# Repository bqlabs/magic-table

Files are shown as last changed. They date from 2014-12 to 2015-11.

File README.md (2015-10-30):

<p align="center">
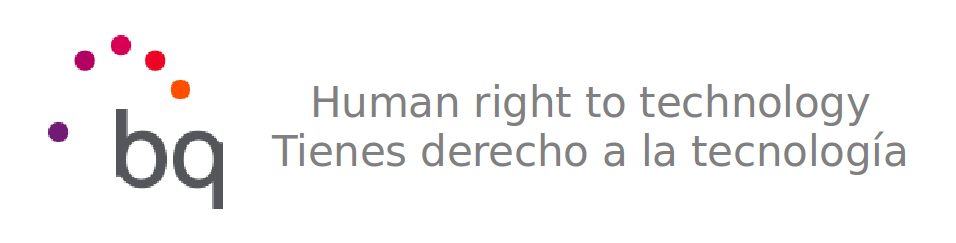
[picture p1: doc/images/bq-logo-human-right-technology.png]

</p>

Magic Table
-------------

HBot-based 2D CNC machine for different applications.

<p align="center">
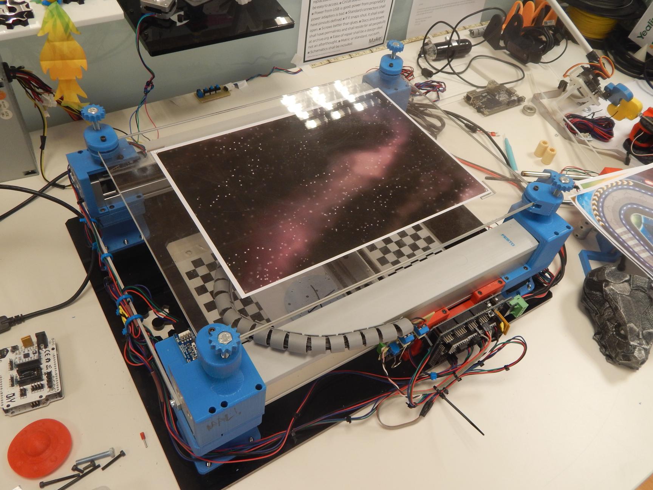
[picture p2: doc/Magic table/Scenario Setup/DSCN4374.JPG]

</p>

# Repository Structure
(Check out each folder's README file for more info on subfolders)

 * /
   * /doc -> Documentation of FESTO hardware parts and tests performed with the machine
   * /firmware ->  Firmware for different embedded devices that that work with the Magic Table
   * /hardware -> Both 3D printable mechanical parts and PCBs for accesories.
   * /software -> Programs to control the Magic Table and use it in different applications.

# Applications developed

## LightPainting
Draw 2D shapes with an RGB light.
<p align="center">
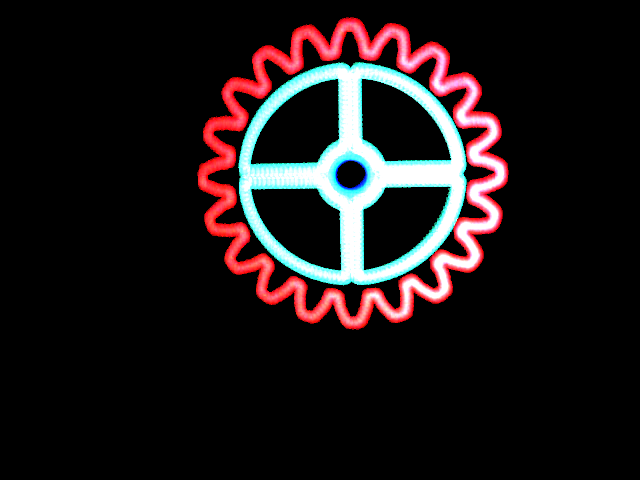
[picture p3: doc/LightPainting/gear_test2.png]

</p>

## Magic Table
Control different pieces and figures with an electromagnet.
<p align="center">
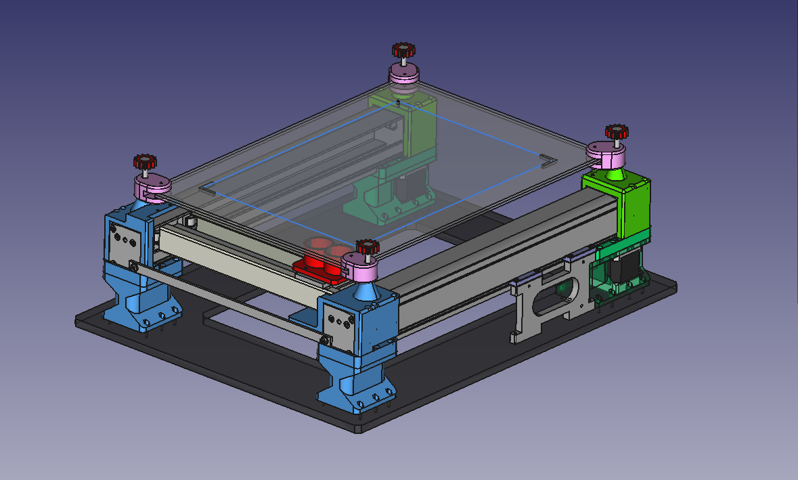
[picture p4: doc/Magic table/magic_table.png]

</p>

# Credits

 * Author: [David Estevez Fernandez](https://github.com/David-Estevez)

# License
<p align="right">

</p>

This machine is licensed under a [Creative Commons Attribution-ShareAlike 4.0 International License](http://creativecommons.org/licenses/by-sa/4.0/). Please read the LICENSE files for more details.

Esta maquina tiene una licencia [Creative Commons Attribution-ShareAlike 4.0 International License](http://creativecommons.org/licenses/by-sa/4.0/). Por favor, lea los ficheros LICENSE para más detalles

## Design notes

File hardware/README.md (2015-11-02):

# Hardware
## Accessories
PCB designs for different accesories, like the etch-a-sketcher or the electromagnet controller board.

## CoreXY Essencials
Set of 3D-printable parts to set the most basic configurations of the magic table

## Light Painting
Set of 3D-printable parts to attach the LED for light paiting applications

## Magic Table
Set of 3D-printable parts to attach the electromagnet and the top cover for the "magic table" applications.

This folder also includes the pieces and backgrounds for each of the "magic table" applications.

## Utils
Different 3D-printable parts to attach accessories such as a webcam to the magic table.

# Z Axis
Set of 3D-printable parts to add a (proof of concept) Z axis.

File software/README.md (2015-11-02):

# Software
## LightPainter
Different Python scripts for light painting applications

## Magic Table
Python software to control the magic table, calibrate it and run demo applications.

It also includes configuration files for each of the applications.

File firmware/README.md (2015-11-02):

# Firmware
## Marlin patch
Patch for Marlin to wait until a position is reached before toggling a GPIO. Instructions to apply the patch can be found inside the folder.

## Etch-a-sketcher
Firmware for the Teensy 3.1 for the "Etch-a-sketcher" peripheral.

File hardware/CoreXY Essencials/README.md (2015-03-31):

# CoreXY Essencials

Parts for the basic CoreXY configuration

## Known bugs

  * The design has an error in the Leg (Upper) BL part, some part that was a dependency was deleted and the dependency is lost. Nevertheless the STL file for that part is correct.

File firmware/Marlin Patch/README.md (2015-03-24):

Patch for Marlin
------------------------

Adds support for waiting for queued movements before toggling GPIOs

To apply patch first clone the Marlin repository:
    $ git clone git@github.com:MarlinFirmware/Marlin.git

Then run the patch command inside the repository:
    $ git am <patch_file>

Note: this patch was applied to commit 512a005. If patching to latest commit fails,
try to patch that one

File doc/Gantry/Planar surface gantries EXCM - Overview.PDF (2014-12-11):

# Overview selected features Planar surface gantry EXCM-30-310-210-KF-W-B-ES

#2226101

Basic configuration
Feature | Value Product type | EXCM series M
Size | 30
Stroke of the X axis | 310 mm
Stroke of the Y-axis | 210 mm
Guide | KF Recirculating ball bearing guide
Motor type | W Without motor
Motor attachment position | B Bottom
Controller | Without
Language of documentation | ES Spanish
03/12/2014 - Subject to change - Festo AG & Co. KG | 1 / 1

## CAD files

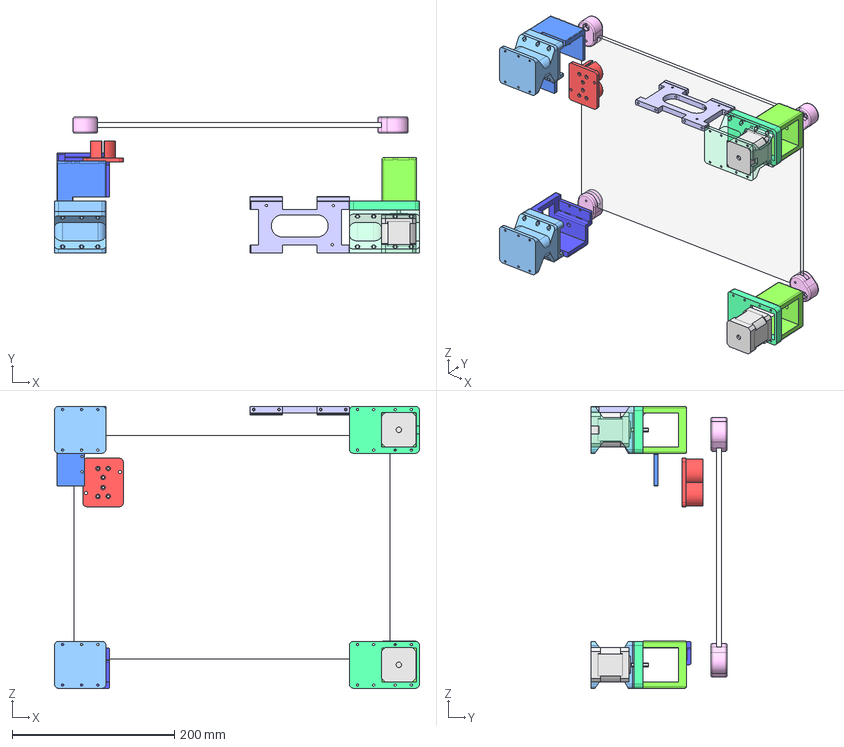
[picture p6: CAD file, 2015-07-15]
hardware/Table Base Holder/Magic Table Assembly.fcstd
450.5 x 168.0 x 348.5 mm
Motor NEMA 17 (47mm) Right
Motor NEMA 17 (40mm) Left
Leg (Upper) Motor [Fillet]
Leg (Body) TR Nice Fillet
Leg (Upper) TR Motor
Leg (Body) BR Nice Fillet
Leg (Upper) BR Endstop holder holes
Leg (Upper) BL [Clone]
Leg (Body) BL Nice Fillet
Arduino Holder Fillet
Support Screw 01 (Top Right)002
Support Up (Top Right)002
Support Screw 02 (Top Right)002
Support Screw 02 (Top Right)001
Support Up (Top Right)001
Support Screw 01 (Top Right)001
Table Holder Base Motor Legs
Clone of Table Holder Base Motor Legs
Table Holder Base Endstop Y
Holder_With_Top_Hole
Magnet_Holder_Hole
Acrylic tabletop (Both)
Attachment
A4 paper
Clone of Attachment
Clone of Attachment001
Clone of Attachment002

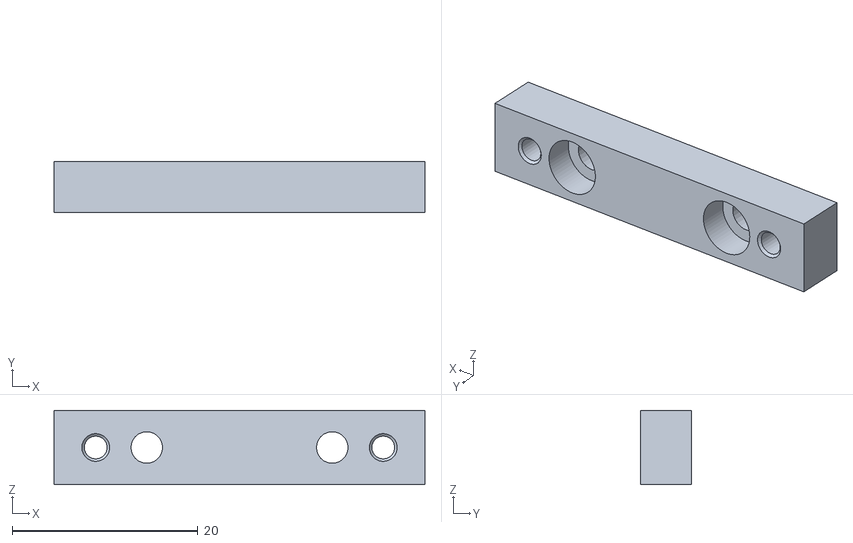
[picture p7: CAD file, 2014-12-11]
doc/Gantry/support_bottom.stl
40.0 x 5.50 x 8.00

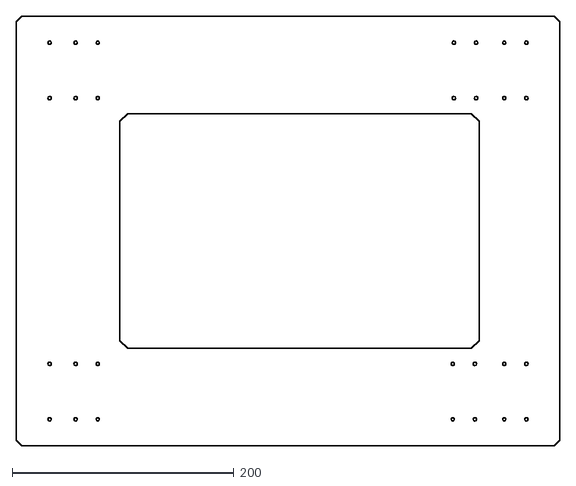
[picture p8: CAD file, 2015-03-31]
hardware/CoreXY Essencials/dxf/base.dxf
490.5 x 388.0

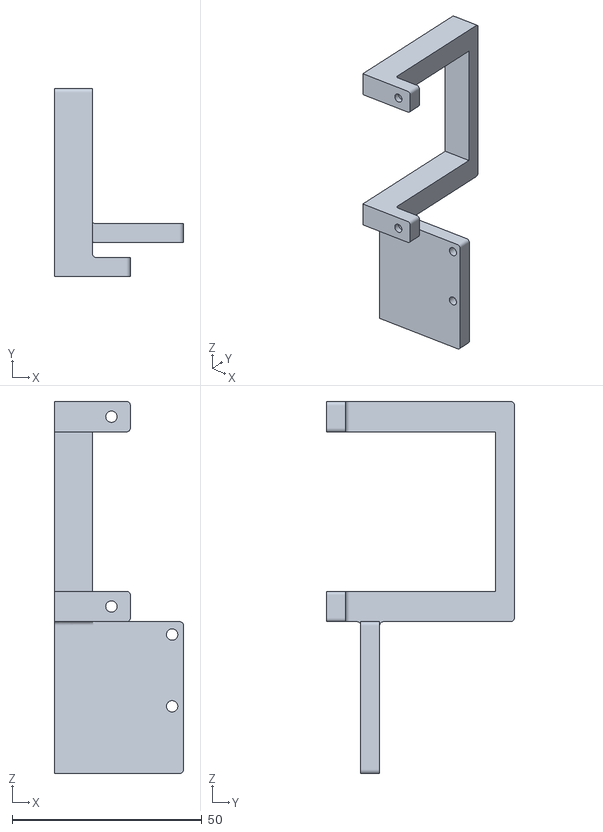
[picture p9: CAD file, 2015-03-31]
hardware/CoreXY Essencials/stl/Endstop Holder Y.stl
34.0 x 49.5 x 98.0

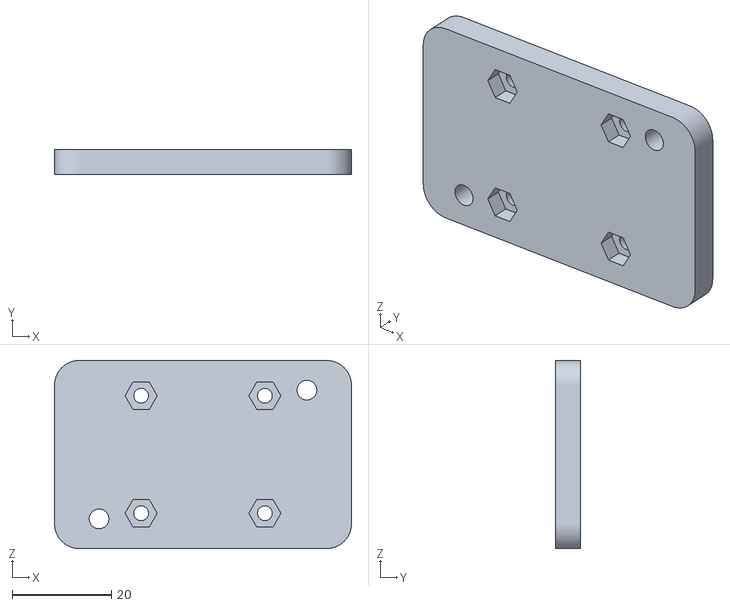
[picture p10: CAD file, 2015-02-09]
hardware/Light Painting/LED holder.stl
60.0 x 5.00 x 38.0

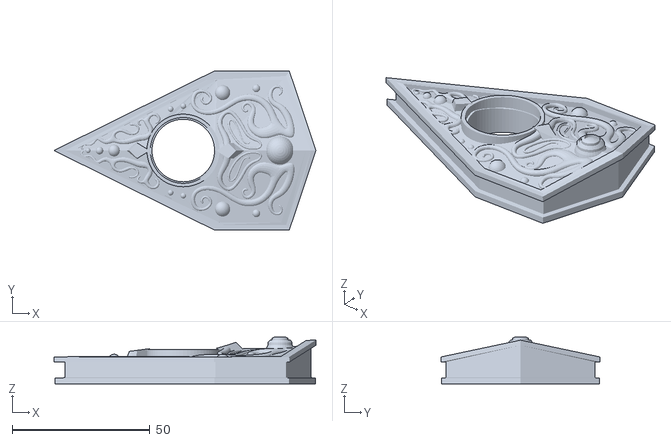
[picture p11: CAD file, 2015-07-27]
hardware/Magic Table/Applications/Ouija/Ouija_Cursor.stl
95.1 x 57.6 x 17.0

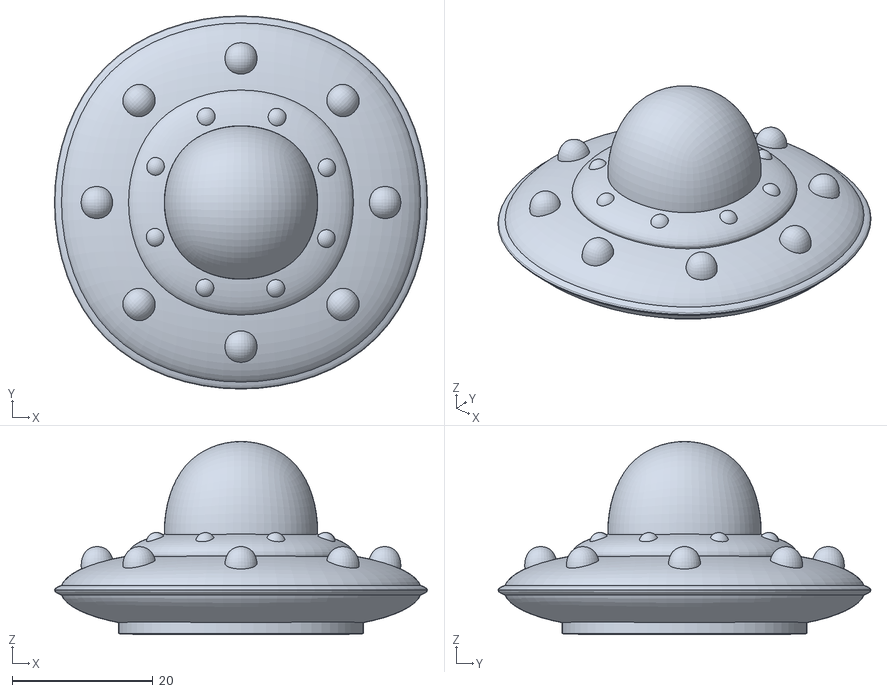
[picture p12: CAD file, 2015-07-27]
hardware/Magic Table/Applications/Space Explorer/UFO.stl
53.0 x 53.0 x 27.5

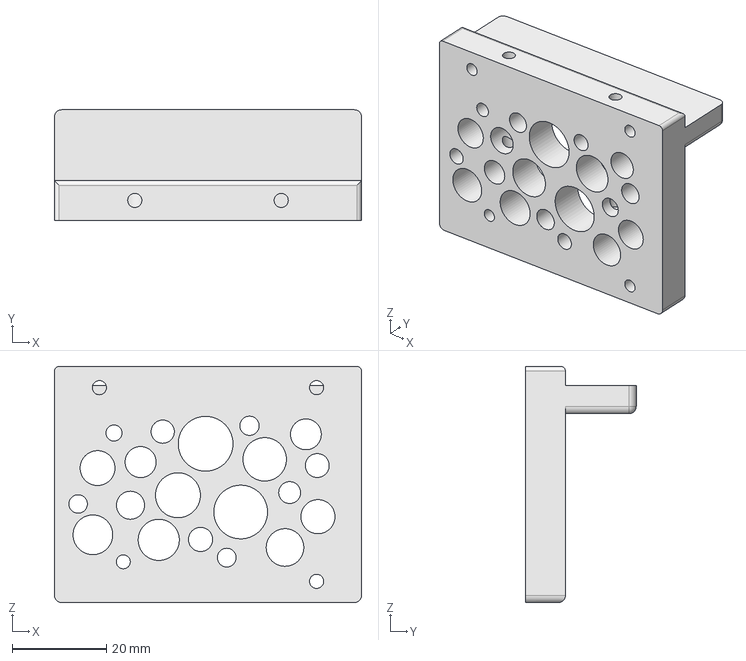
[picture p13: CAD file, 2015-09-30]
hardware/Magic Table/Electromagnet Controller Holder/Electromagnet Controller Holder.fcstd
65.0 x 23.4 x 50.0 mm

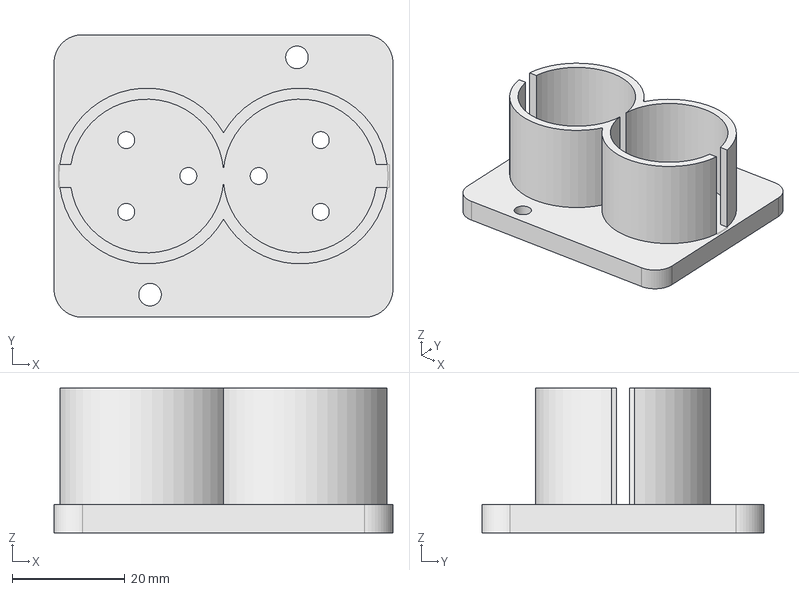
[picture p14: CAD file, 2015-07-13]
hardware/Magic Table/Electromagnet Holder/Electromagnet Holder Double.step
60.0 x 50.0 x 25.6 mm

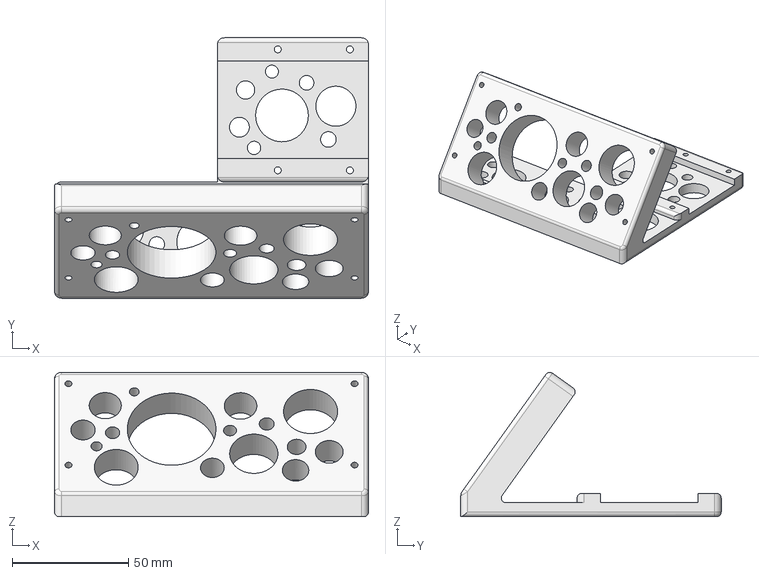
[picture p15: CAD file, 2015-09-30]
hardware/Magic Table/Screen Holder/Screen Holder.fcstd
135.0 x 112.0 x 62.1 mm

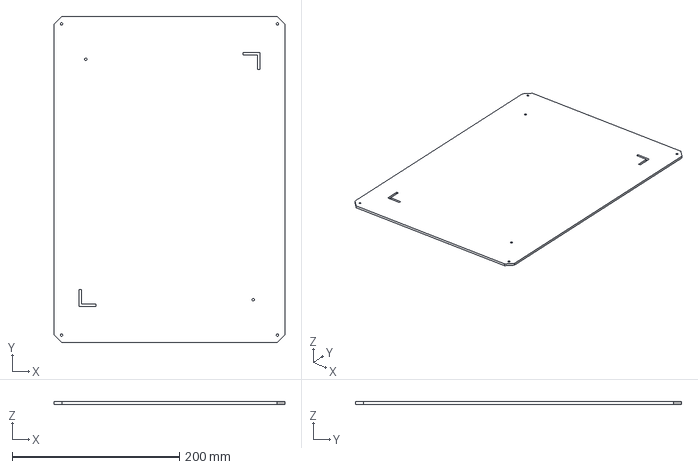
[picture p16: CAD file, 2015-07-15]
hardware/Magic Table/Table Base Holder/Acrylic Base.fcstd
276.0 x 390.0 x 3.00 mm

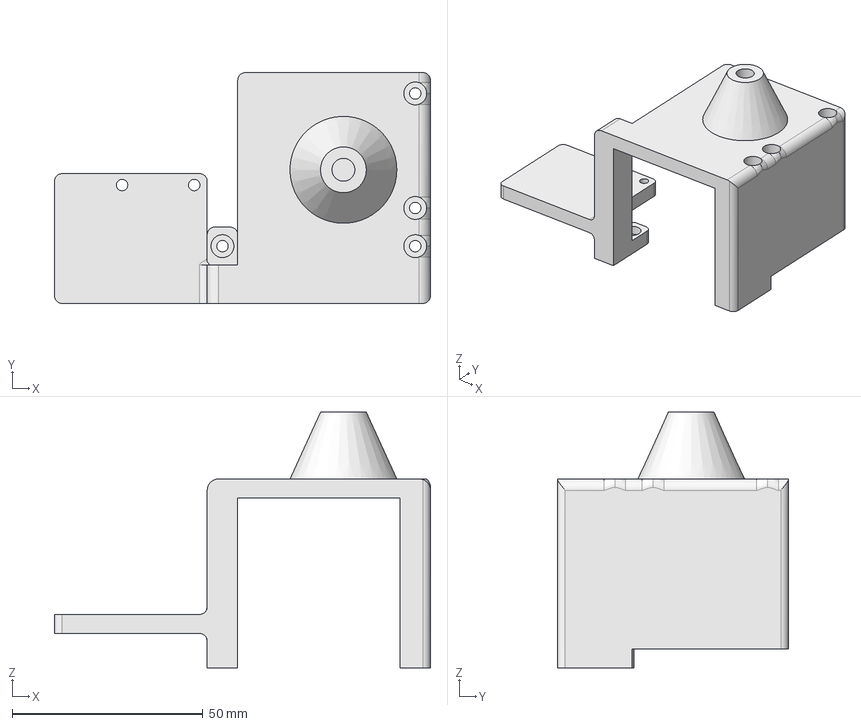
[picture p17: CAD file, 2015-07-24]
hardware/Magic Table/Table Base Holder/step/Table Holder Base Endstop Y.step
98.5 x 60.5 x 67.0 mm

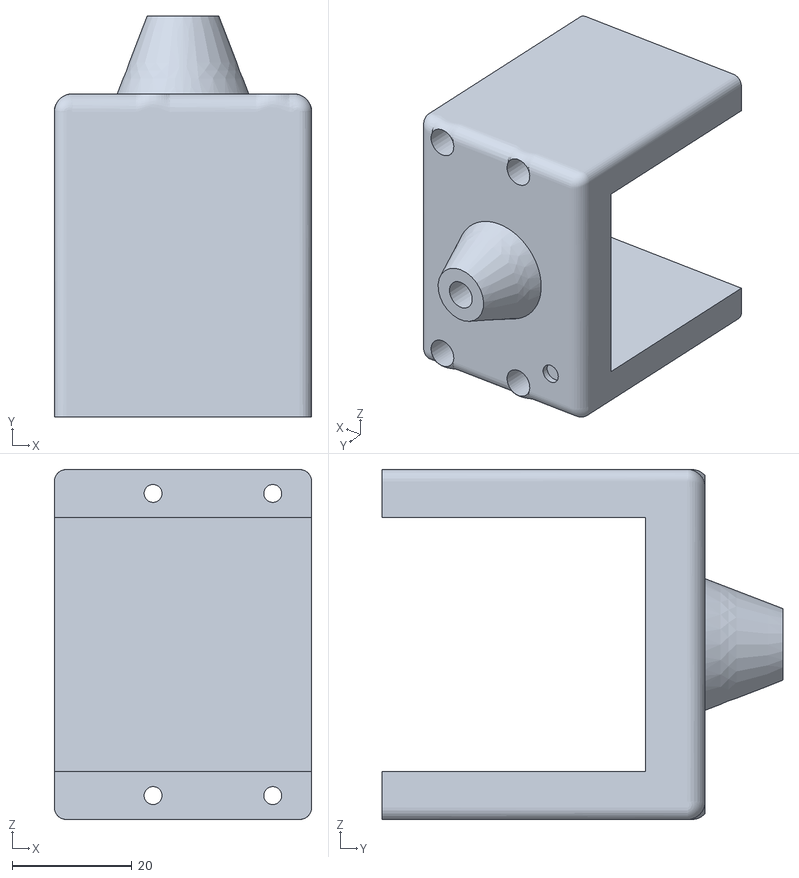
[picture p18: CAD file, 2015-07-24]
hardware/Magic Table/Table Base Holder/stl/Table Holder Base Motor Leg Right.stl
43.0 x 67.0 x 58.5

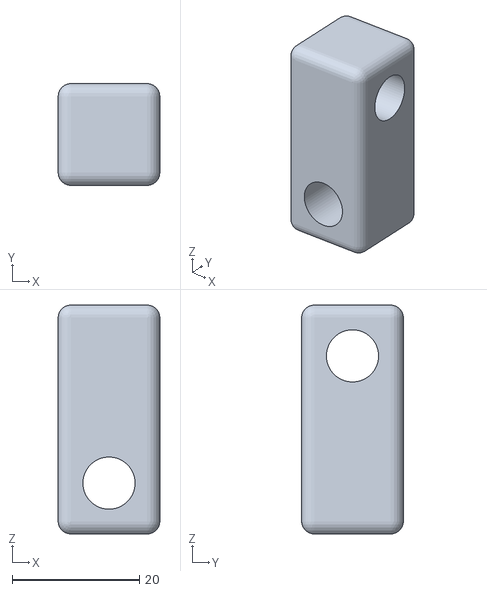
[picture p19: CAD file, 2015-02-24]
hardware/Utils/M8 connector.stl
16.0 x 16.0 x 36.0

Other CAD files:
hardware/Magic Table/Electromagnet Holder/stl/electromagnet holder dual.stl
hardware/Utils/Camera Holder/Camera.fcstd
hardware/Z Axis/experimental_test.fcstd
hardware/CoreXY Essencials/stl/Endstop Holder X.stl
doc/Coupling/530085_EAMC-B-15-22-5-5_2_03.stp
doc/Gantry/2226101_EXCM-30-310-210-KF-W-B-ES_2_03.stp
hardware/CoreXY Essencials/stl/Arduino Holder.stl
hardware/CoreXY Essencials/stl/Gantry Connector Upper.stl
hardware/CoreXY Essencials/stl/Leg (Body) Bottom Legs.stl
hardware/CoreXY Essencials/stl/Leg (Body) Motor Legs.stl
hardware/CoreXY Essencials/stl/Leg (Upper) Bottom Legs.stl
hardware/CoreXY Essencials/stl/Leg (Upper) Motor Legs.stl
hardware/Light Painting/Cable holder.stl
hardware/Magic Table/Applications/Space Explorer/Path.stl
hardware/Magic Table/Electromagnet Controller Holder/Electromagnet Controller Holder.stl
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

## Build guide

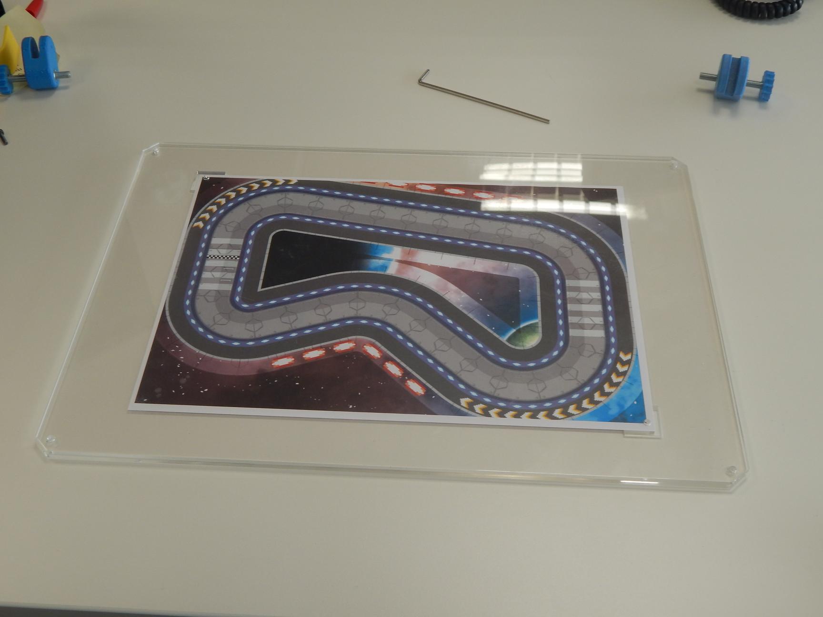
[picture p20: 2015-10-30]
doc/Magic table/Scenario Setup/DSCN4384.JPG

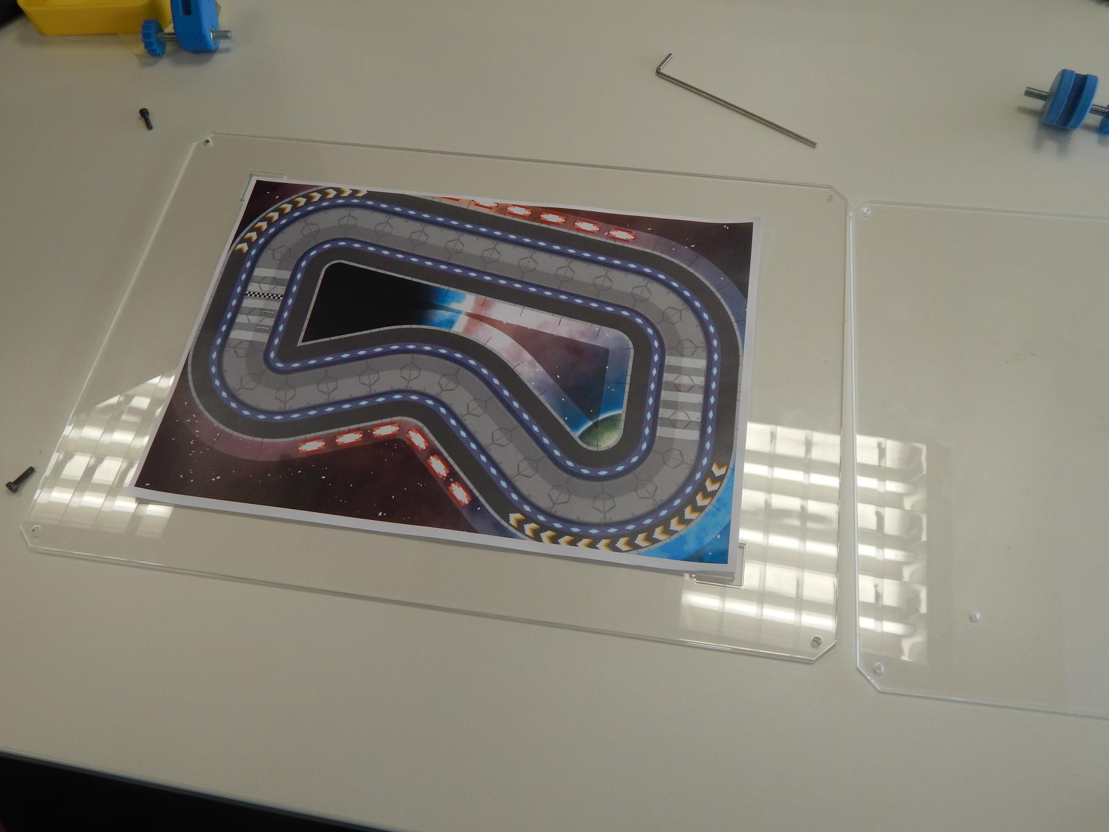
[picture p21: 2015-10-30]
doc/Magic table/Scenario Setup/DSCN4383.JPG

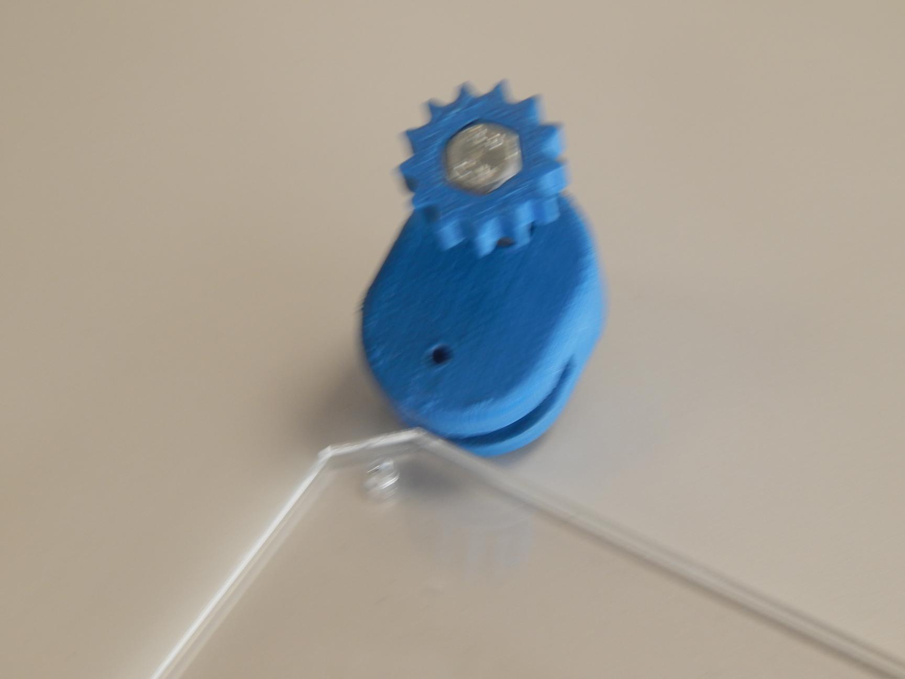
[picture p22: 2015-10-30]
doc/Magic table/Scenario Setup/DSCN4379.JPG

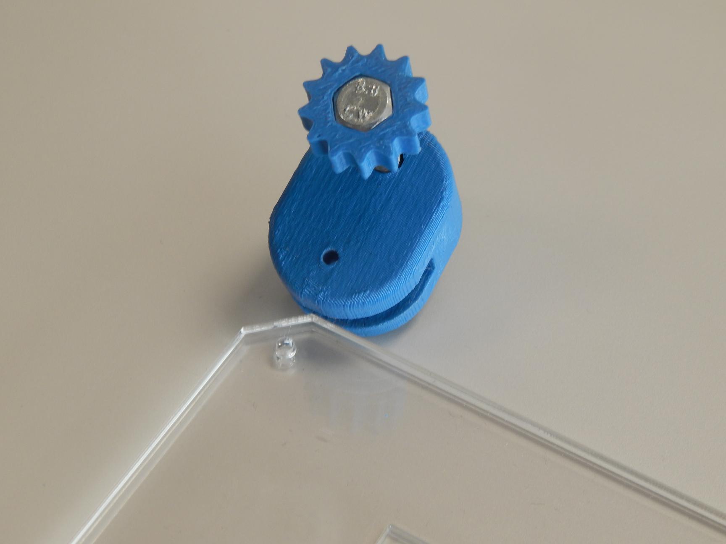
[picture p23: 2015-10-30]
doc/Magic table/Scenario Setup/DSCN4380.JPG

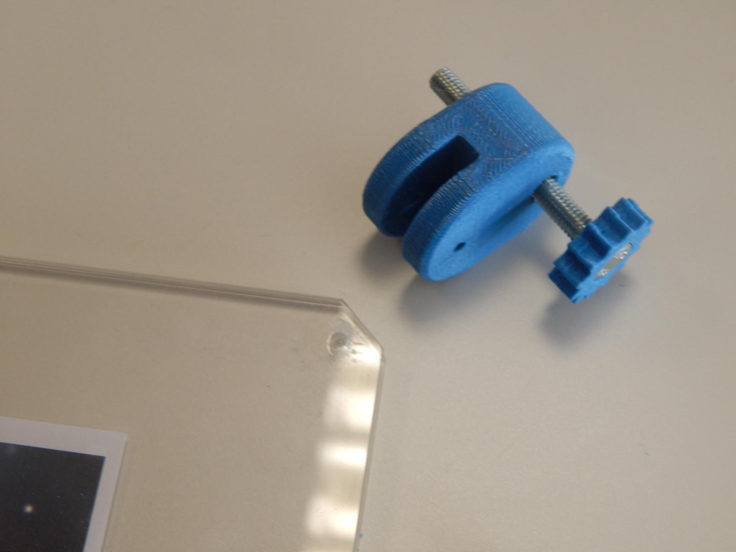
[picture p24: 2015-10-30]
doc/Magic table/Scenario Setup/DSCN4377.JPG

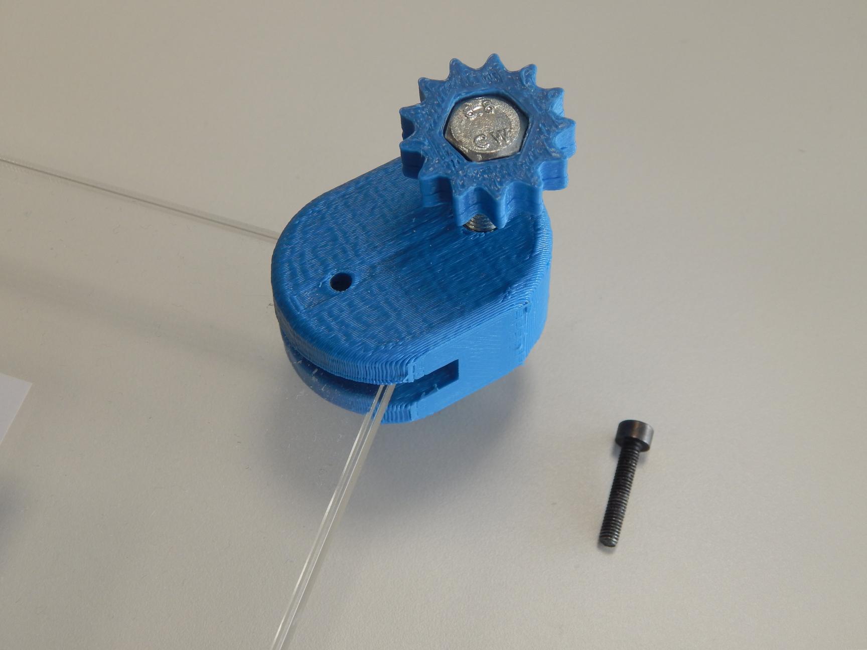
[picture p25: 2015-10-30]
doc/Magic table/Scenario Setup/DSCN4376.JPG

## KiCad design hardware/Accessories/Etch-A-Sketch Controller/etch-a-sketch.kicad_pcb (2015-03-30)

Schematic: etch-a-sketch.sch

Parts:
BOARD1: BOARD_TEENSY_3.1
C1, C2, C3, C4: C
D1, D3: GREEN
D2, D4: RED
EN1, EN2: ENCODER_5_PINS
R1, R2, R3, R4, R5, R6, R7, R8, R9, R10, R11, R12: R
SW1, SW2, SW3, SW4: DPST

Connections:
/D0: BOARD1.2, C2.1, R4.2
/D1: BOARD1.3, C1.1, R3.2
/D2: BOARD1.4, EN1.4
/D9: BOARD1.11, SW3.3
/D10: BOARD1.12, SW1.3
/D11: BOARD1.13, D3.1 (A)
/D12: BOARD1.14, D1.1 (A)
/D14: BOARD1.16, D2.1 (A)
/D15: BOARD1.17, D4.1 (A)
/D16: BOARD1.18, SW2.3
/D17: BOARD1.19, SW4.3
/D21: BOARD1.23, EN2.4
/D22: BOARD1.24, C4.1, R8.2
/D23: BOARD1.25, C3.1, R7.2
GND: BOARD1.1, C1.2, C2.2, C3.2, C4.2, EN1.2, EN1.5, EN1.SHLD, EN2.2, EN2.5, EN2.SHLD, R9.2, R10.2, R11.2, R12.2, SW1.2, SW2.2, SW3.2, SW4.2
unnamed: D2.2 (K), R10.1
unnamed: D4.2 (K), R12.1
unnamed: D3.2 (K), R11.1
unnamed: D1.2 (K), R9.1
unnamed: EN2.1, R5.1, R7.1
unnamed: EN1.1, R1.1, R3.1
unnamed: EN1.3, R2.1, R4.1
unnamed: EN2.3, R6.1, R8.1
VCC: BOARD1.26, R1.2, R2.2, R5.2, R6.2

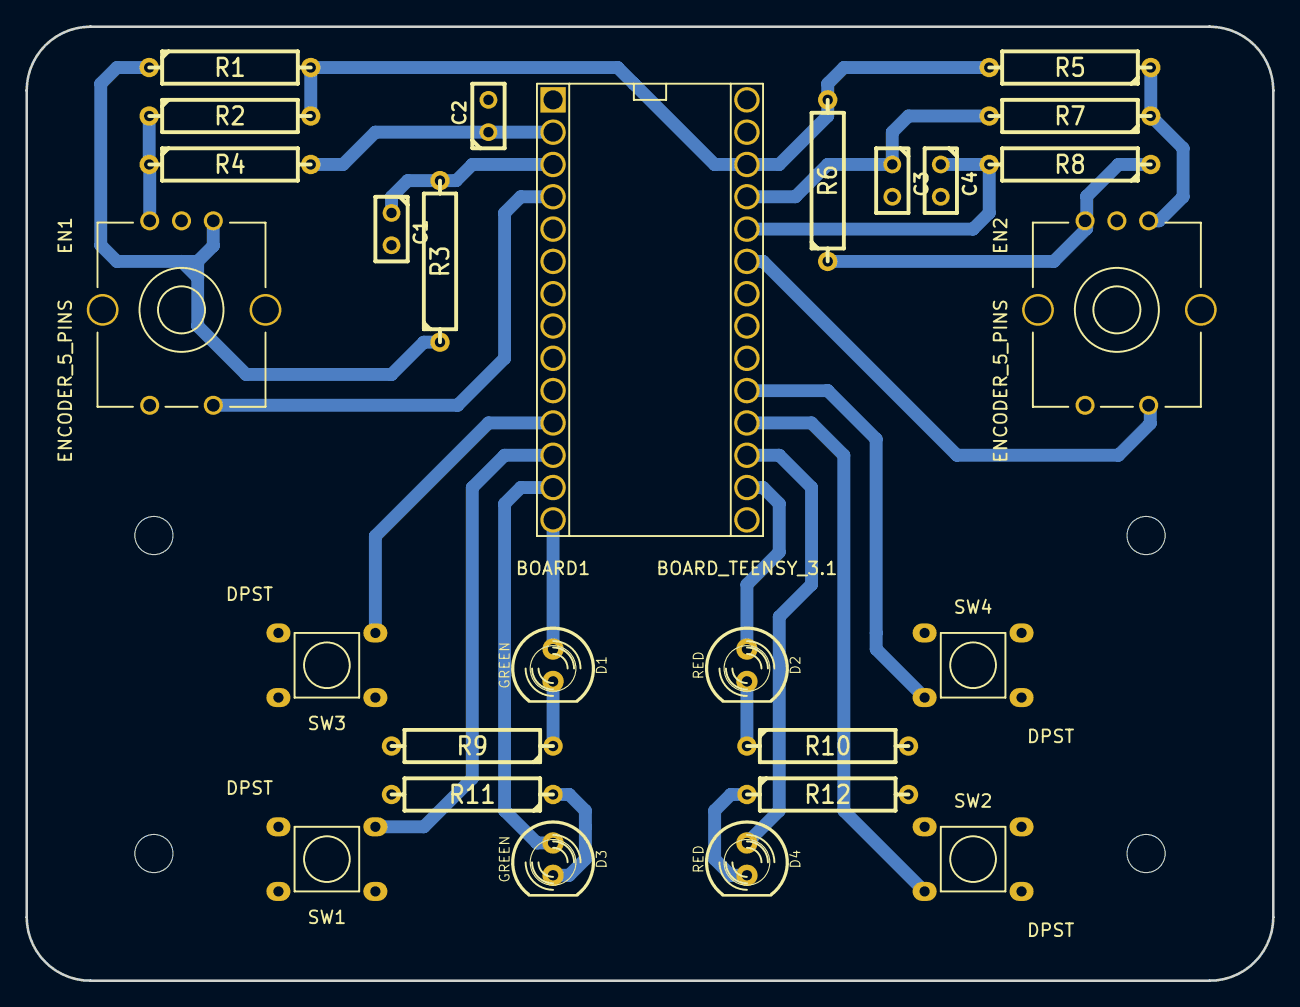
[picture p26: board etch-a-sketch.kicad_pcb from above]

Board: 2 copper layers, 98.0 x 75.0 mm, 31 parts (0 on the bottom side), 24 nets.

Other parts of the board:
Mechanical_drill_3mm, Mechanical_drill_3mm#2, Mechanical_drill_3mm#3, Mechanical_drill_3mm#4: Mechanical_drill_3mm

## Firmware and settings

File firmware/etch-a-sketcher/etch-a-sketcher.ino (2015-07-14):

/* 
  etch-a-sketcher 
  -----------------------------------
  Creative computer interface
  
  author: def
*/

#include <Encoder.h>
#include <Bounce.h>

//-- Pins
const int boardLedPin = 13;
const int userLedPins[4] = {12, 14, 11, 15};

const int encoderLeftButtonPin = 2;
const int encoderRightButtonPin = 21;

const int buttonPins[4] = {10, 16, 9, 17};


//-- Global objects:
Encoder knobLeft(1, 0);
Encoder knobRight(23, 22);

Bounce encoderLeftButton  = Bounce(encoderLeftButtonPin, 10);
Bounce encoderRightButton = Bounce(encoderRightButtonPin, 10);

Bounce buttons[4] = { Bounce(buttonPins[0], 10),
                      Bounce(buttonPins[1], 10),
                      Bounce(buttonPins[2], 10),
                      Bounce(buttonPins[3], 10)};

//-- State-related variables & defines
#define MODE_0 0  //-- Emulate cursor position
#define MODE_1 1  //-- Emulate mouse scroll
#define MODE_2 2  //-- Emulate keyboard arrows
#define MODE_3 3  //-- ?

int state = MODE_0;

//-- Encoder position related variables
long positionLeft  = 0;
long positionRight = 0;

void setup() 
{  
  //-- Buttons & leds
  pinMode(boardLedPin, OUTPUT);
  
  for(int i = 0; i < 4; i++)
  {
    pinMode(userLedPins[i], OUTPUT);
    pinMode(buttonPins[i], INPUT_PULLUP);
  }
  
  //-- Encoder pins config
  pinMode(encoderLeftButtonPin, INPUT_PULLUP);
  pinMode(encoderRightButtonPin, INPUT_PULLUP);
  
  //-- Keyboard, mouse, and other HID init
  Keyboard.begin();
  Mouse.begin();
  
  //-- Init lights sequence
  for(int i = 0; i < 4; i++)
  {
    digitalWrite(userLedPins[i], HIGH);   // set the LED on
    delay(200);                  // wait for a second
    digitalWrite(userLedPins[i], LOW);    // set the LED off
    delay(200);                  // wait for a second
  }
  
  //-- Initial button update (to cleanup initial rising edge detect (?))
  encoderLeftButton.update();
  encoderRightButton.update();
  
  for(int i = 0; i < 4; i++)
    buttons[i].update();
  
}


void loop() 
{
  //-- Update button status
  encoderLeftButton.update();
  encoderRightButton.update();
  
  for(int i = 0; i < 4; i++)
    buttons[i].update();
    

  
  //-- Things to be done on each state:
  if (state == MODE_0)
  {
    mode0();
  }
  else if (state == MODE_1)
  {
      mode1();
  }
  else if (state == MODE_2)
  {
      mode2();
  }
  else if (state == MODE_3)
  {
    //-- Things to do here
    digitalWrite(userLedPins[0], LOW);
    digitalWrite(userLedPins[1], LOW);
    digitalWrite(userLedPins[2], LOW);
    digitalWrite(userLedPins[3], HIGH);
  }
  
  //-- State transitions:
  for(int i = 0; i < 4; i++)
    if (buttons[i].risingEdge())
    {
      //-- Change state variable & reset knobs
      state = i;
      positionLeft  = 0;
      positionRight = 0;
      knobLeft.write(0);
      knobRight.write(0);
    }
}

void mode0()
{
    //-- Mode 0: scroll + TAB
    //----------------------------------
    digitalWrite(userLedPins[0], HIGH);
    digitalWrite(userLedPins[1], LOW);
    digitalWrite(userLedPins[2], LOW);
    digitalWrite(userLedPins[3], LOW);

    //-- Read encoders
    long newLeft, newRight;
    newLeft = knobLeft.read();
    newRight = knobRight.read();
    
    //-- Do things if encoders where moved
  
    if (newLeft > positionLeft)
    {
      //-- Left turned right
      Mouse.move(0, 0, 5);  
    }
    else if (newLeft < positionLeft)
    {
      //-- Left turned left
      Mouse.move(0, 0, -5);  
    }
    
    if (newRight > positionRight)
    {
      //-- Right turned right
      Keyboard.press(KEY_LEFT_SHIFT);
      Keyboard.press(KEY_TAB);
      digitalWrite(boardLedPin, HIGH);
      delay(100);
      Keyboard.release(KEY_TAB);
      Keyboard.release(KEY_LEFT_SHIFT);
      digitalWrite(boardLedPin, LOW);      
    }
    else if (newRight < positionRight)
    {
      //-- Right turned left
      Keyboard.press(KEY_TAB);
      digitalWrite(boardLedPin, HIGH);
      delay(100);
      Keyboard.release(KEY_TAB);
      digitalWrite(boardLedPin, LOW);     
    }

    //-- Update encoder counters
    positionLeft = newLeft;
    positionRight = newRight;
    delay(50);          
    
}
void mode1()
{
    //-- Mode 1: position control
    //----------------------------------
    digitalWrite(userLedPins[0], LOW);
    digitalWrite(userLedPins[1], HIGH);
    digitalWrite(userLedPins[2], LOW);
    digitalWrite(userLedPins[3], LOW);
    
    //-- Read encoders
    long newLeft, newRight;
    newLeft = knobLeft.read();
    newRight = knobRight.read();
    
    //-- Do things if encoders where moved
  
    if (newLeft > positionLeft)
    {
      //-- Left turned right
      Mouse.move(-5, 0, 0);  
    }
    else if (newLeft < positionLeft)
    {
      //-- Left turned left
      Mouse.move(5, 0, 0);  
    }
      
    if (newRight > positionRight)
    {
      //-- Right turned right
      Mouse.move(0, 5, 0);        
    }
    else if (newRight < positionRight)
    {
      //-- Right turned left
      Mouse.move(0, -5, 0);       
    }
    
    
    //-- Update encoder counters
    positionLeft = newLeft;
    positionRight = newRight;
    delay(50);      
}
void mode2()
{
    //-- Mode 2: arrow control
    //----------------------------------
    digitalWrite(userLedPins[0], LOW);
    digitalWrite(userLedPins[1], LOW);
    digitalWrite(userLedPins[2], HIGH);
    digitalWrite(userLedPins[3], LOW);
    
    //-- Read encoders
    long newLeft, newRight;
    newLeft = knobLeft.read();
    newRight = knobRight.read();
    
    //-- Do things if encoders where moved
  
    if (newLeft > positionLeft)
    {
      //-- Left turned right
      Keyboard.press(KEY_LEFT_ARROW);
      digitalWrite(boardLedPin, HIGH);
      delay(100);
      Keyboard.release(KEY_LEFT_ARROW);
      digitalWrite(boardLedPin, LOW);    
    }
    else if (newLeft < positionLeft)
    {
      //-- Left turned left
      Keyboard.press(KEY_RIGHT_ARROW);
      digitalWrite(boardLedPin, HIGH);
      delay(100);
      Keyboard.release(KEY_RIGHT_ARROW);
      digitalWrite(boardLedPin, LOW);     
    }
      
    if (newRight > positionRight)
    {
      //-- Right turned right
      Keyboard.press(KEY_UP_ARROW);
      digitalWrite(boardLedPin, HIGH);
      delay(100);
      Keyboard.release(KEY_UP_ARROW); 
      digitalWrite(boardLedPin, LOW);        
    }
    else if (newRight < positionRight)
    {
      //-- Right turned left
      Keyboard.press(KEY_DOWN_ARROW);
      digitalWrite(boardLedPin, HIGH);
      delay(100);
      Keyboard.release(KEY_DOWN_ARROW);
      digitalWrite(boardLedPin, LOW);        
    }
    
    //-- Update encoder counters
    positionLeft = newLeft;
    positionRight = newRight;
    delay(100);      
}

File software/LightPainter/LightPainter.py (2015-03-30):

# Import instructions
from Instruction.StartInstruction import StartInstruction
from Instruction.TravelInstruction import TravelInstruction
from Instruction.PaintInstruction import PaintInstruction
from Instruction.EndInstruction import EndInstruction

# Import iterators
from ImageIterator.RowIterator import RowIterator

# Import image transformations
from Utils.transform_image import transform_image

# Other imports
import numpy as np
import cv2
import optparse

__author__ = 'def'

class LightPainter:
    def __init__(self):
        # Configuration of the physical parameters
        #----------------------------------------------------------------------------------------------------
        # CoreXY dimensions
        self.total_length = 310
        self.total_width = 210

        # Working area (webcam field of view)
        # note: working_length and width need to be recalculated if they are to be configured externally
        self.working_upper_left = (54.70, 216.90)
        self.working_lower_right = (144.30, 91.90)

        # LED parameters:
        self.max_led_value = 30 # From 0 to 255
        self.led_resolution = 1

        # LED stepping (resolution of the real grid in mm) [this uses the working area frame of reference]
        self.x_step_resolution = 5
        self.y_step_resolution = 5

        # Generate other parameters
        #----------------------------------------------------------------------------------------------------
        self.working_length = None
        self.working_width = None
        self.src_img_height = None
        self.src_img_width = None
        self.src_img_max_value = None

        self.configure()

    # CoreXY configuration from parameters
    def configure(self):
        """
            Calculate parameters from coreXY configuration data
        """
        # Working area (webcam field of view)
        self.working_length = abs( self.working_upper_left[1] - self.working_lower_right[1] )
        self.working_width = abs( self.working_upper_left[0] - self.working_lower_right[0] )

        # Calculations for the allowed origin image (max) dimensions
        self.src_img_height = int(self.working_width / self.x_step_resolution)
        self.src_img_width = int(self.working_length / self.y_step_resolution)

    # Functions related to changing the frame of reference of points
    def workingArea2CoreXYCoord(self, working_area_point, working_area_led_value = 0):
        """
            Changes coordinates from working area to CoreXY frame of reference
        """
        x = working_area_point[0] + self.working_upper_left[0]
        y = working_area_point[1] + self.working_lower_right[1]
        led_value = working_area_led_value

        return [ (x, y), led_value]

    def imageCoor2workingAreaCoor(self, image_point, pixel = 0):
        """
            Changes coordinates from working area to CoreXY frame of reference
        """
        x = self.working_width - image_point[1] * self.x_step_resolution
        y = self.working_length - image_point[0] * self.y_step_resolution
        new_pixel = np.floor( np.true_divide(pixel * np.true_divide(self.max_led_value, 255), self.led_resolution)) * self.led_resolution

        return [ (x, y), new_pixel]

    # Processing a image to get the gcode
    def process_image_to_instructions(self, image):
        """
            Gets an image and processes it to generate the gcode
        """
        # Transform image to allowed dimensions
        new_image = transform_image(image, self.src_img_width, self.src_img_height, 3)
        cv2.imwrite('debug.png', new_image)

        # Create iterator(s)
        it_origin = RowIterator(new_image)
        it_dest = RowIterator(new_image)
        it_dest.next()

        # Generate instructions
        instructions = []
        instructions.append(StartInstruction())

        for (origin_point, origin_value), (dest_point, dest_value)  in zip(it_origin, it_dest):
            # Coordinate transformation for the current points:
            wa_origin_point, wa_origin_value = self.imageCoor2workingAreaCoor(origin_point, origin_value)
            abs_origin_point, abs_origin_value = self.workingArea2CoreXYCoord(wa_origin_point, wa_origin_value)

            wa_dest_point, wa_dest_value = self.imageCoor2workingAreaCoor(dest_point, dest_value)
            abs_dest_point, abs_dest_value = self.workingArea2CoreXYCoord(wa_dest_point, wa_dest_value)

            # Generate different instructions depending of color
            if sum(abs_origin_value == 0) == abs_origin_value.size:
                # Black pixel -> travel instruction
                new_instruction = TravelInstruction(abs_origin_point, abs_dest_point)

                # Try to accumulate travel instructions
                try:
                    if instructions[-1].type == 'TravelInstruction':
                        instructions[-1].join(new_instruction)
                except:
                    instructions.append(new_instruction)

            else:
                new_instruction = PaintInstruction(abs_origin_point, abs_dest_point, abs_origin_value)
                instructions.append(new_instruction)



        instructions.append(EndInstruction())

        return instructions


    def process_image_to_gcode(self, image):
        """
            Gets an image and processes it to generate the gcode
        """
        # Generate instructions
        instructions = self.process_image_to_instructions(image)

        # Generate gcode
        gcode = ''
        for instruction in instructions:
            gcode += instruction.generate_code()

        return gcode


# Test #1 : trajectory generation
def x(t, r = 45):
    return  r * np.cos(t)

def y(t, r = 45):
    return  r * np.sin(t)

def test1(output_file):
        # Generate points of circle:
    t_array = np.arange(0, 10*np.pi, 0.1)
    points = [ ( x(t)+100, y(t)+150) for t in t_array ]

    # Generate instructions
    instructions = []
    instructions.append(StartInstruction())

    #instructions.append(TravelInstruction((0,0), (100, 100)))
    for origin, dst in zip(points[:-1], points[1:]):
         instructions.append(TravelInstruction(origin, dst))

    instructions.append(EndInstruction())

    # Generate gcode
    gcode = ''
    for instruction in instructions:
        gcode += instruction.generate_code()

    with open(output_file, 'w') as f:
        f.write(gcode)
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

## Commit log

2014-12-11 Initial commit.
    [2226101_EXCM-30-310-210-KF-W-B-ES_2_03.stp, 530085_EAMC-B-15-22-5-5_2_03.stp, assembly.fcstd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]
2014-12-12 Added test for supports.
    [assembly.fcstd]
2014-12-12 Add all supports.
    [assembly.fcstd]
2014-12-12 Minor changes
    [assembly.fcstd]
2014-12-15 Added firsts steps of bottom left leg (upper part of the leg)
    [assembly.fcstd]
2014-12-15 Finished upper part of the bottom left leg
    [assembly.fcstd]
2014-12-16 Leg body (bottom left) sketch finished.
    [assembly.fcstd]
2014-12-19 Added both bottom legs.
    [assembly.fcstd]
2014-12-19 Modified tolerances of bottom legs
    [assembly.fcstd]
2014-12-22 Added motor leg top part
    [assembly.fcstd]
2014-12-22 Add screw head holes to leg top part.
    [assembly.fcstd]
2014-12-22 Motor support leg added.
    [assembly.fcstd]
2014-12-22 Add both motor legs.
    [assembly.fcstd]
2014-12-23 Add v2 motor support. Add base sketch.
    [assembly.fcstd]
2014-12-23 Add chamfered base.
    [assembly.fcstd]
2014-12-30 Correct "Motor Body Leg" part with the correct dimensions.
    Changes:
    - Add correct NEMA 17 model (47mm)
    - Update motor body leg part
    - Started to modify top part
    [assembly.fcstd]
2014-12-30 Fix Leg Motor Top part
    - Add extra holes to attach supports
    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
    [assembly.fcstd]
2014-12-30 Update base position
    [assembly.fcstd]
2014-12-30 Completed remaining legs
    [assembly.fcstd]
2014-12-30 Start creating the endstop holder
    [assembly.fcstd]
2015-01-12 Base sketch of the endstop holder (now really)
    [assembly.fcstd]
2015-01-12 Endstop holder and leg top part finished
    [assembly.fcstd]
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2015-02-05 Arduino holder added and tested.
    [assembly.fcstd]
2015-02-09 Add stl files for the CoreXY basic functionality
    [Arduino Holder.stl, Cable holder.stl, Endstop Holder.stl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]
2015-02-09 Add base file for laser cutting
    [Base.dxf]
2015-02-09 Start working on Ligh Painting code
    Add functions to reduce image dimensions and depth, prior to 'slicing'
    [BOM.ods]
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2015-02-24 Backup of some stl files in development
    [Camera_holder.stl, Camera_holder_v2.stl, Camera_holder_v3.stl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]
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2015-03-03 Add checking ok messages (not working yet)
    [CoreXY.py]
2015-03-10 Create endstop holder for X axis (draft)
    [Endstop Holder X.stl]
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2015-03-24 Solve bug (-1 is used for not found in string, not 1)
    [CoreXY.py]
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2015-03-24 Controller no longer needed (now it is done from modified Marlin)
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2015-03-25 Corrected issue with LED colors (BGR vs RGB)
    [LightPainter.py]
2015-03-25 Add schematic for etch-a-sketch accessory
    [etch-a-sketch.sch]
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2015-03-26 Add netlist and component association
    [etch-a-sketch.sch]
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2015-03-30 Add encoder with gnd shield connection.
    [etch-a-sketch.kicad_pcb, etch-a-sketch.sch]
2015-03-30 Add version adapted to be manufatured in cyclone
    [etch-a-sketch_cyclone.kicad_pcb]
2015-03-30 Fixed coordinate frame bug (as I changed the endstop position)
    [LightPainter.py]
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2015-03-31 Fix and place endstop holders
2015-03-31 Move files to more logical place
    [Arduino Holder.stl, Endstop Holder X.stl, Endstop Holder Y.stl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]
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2015-03-31 Add manufacturing file for base
    [base.dxf]
2015-03-31 Move M8 connectors to Utils
    [M8 connector long.stl, M8 connector.stl, M8 threaded rod holder.stl]
2015-03-31 Move files to more coherent places
    [Base.dxf, Cable holder.stl, Camera.fcstd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]
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2015-05-13 Add electromagnet holder (single and dual)
    [electromagnet holder dual.stl, electromagnet holder v2.stl, electromagnet holder.stl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]
2015-05-14 Add schematic for electromagnet controller board
    [Electromagnet Controller.sch]
2015-05-14 Remove versioning outside CVS
    [electromagnet holder v2.stl, electromagnet holder.stl]
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2015-06-17 Motor Holder almost finished (Top part)
    [experimental_test.fcstd]
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2015-07-09 Add Table holder Motor Leg and Endstop Y Leg
    [Table Holder Base Endstop Y.fcstd, Table Holder Base Motor Legs.fcstd]
2015-07-13 Add Table holder for X endstop side
    [Table Holder Base Endstop X.fcstd]
2015-07-13 Add assembly elements to magic table assembly
    [Electromagnet Holder Double.step, Magic Table Assembly.fcstd, Table Holder Attachment.step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]
2015-07-14 Add acrylic surface to magic table
    [Magic Table Assembly.fcstd, Table Holder Attachment.fcstd, Table Holder Attachment.step]
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2015-07-15 Add Acrylic Table to Assembly
    [Magic Table Assembly.fcstd]
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2015-07-17 Add M6x50 screw model
    [M6x50 Screw.fcstd, M6x50 Screw.step]
2015-07-17 Update top hole in Table Holder Endstop X
    [Table Holder Base Endstop X.fcstd, Table Holder Base Endstop X.step]
2015-07-17 Update top hole in Table Holder Endstop Y
    [Table Holder Base Endstop Y.fcstd, Table Holder Base Endstop Y.step]
2015-07-17 Modify Attachments to fit acrylic
    [Table Holder Attachment (Endstop Side).step]
2015-07-17 Modify top hole in Table Holder Base for Motor Legs
    [Table Holder Base Motor Legs.fcstd, Table Holder Base Motor Legs.step]
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2015-07-21 Add test server in CherryPy
    [M6x50 Screw.step, Table Holder Attachment (Endstop Side).step, Table Holder Attachment.step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]
2015-07-24 Modify Endstop holder Y axis wing height
    [Table Holder Base Endstop Y.step, Table Holder Base Endstop Y.stl]
2015-07-24 Add stl files to repository, clean repo
    [Acrylic Base (Bottom).dxf, Acrylic Base (Bottom).step, Acrylic Base (Top).dxf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]
2015-07-24 Add files for knob
    [Table Holder Knob.fcstd]
2015-07-27 Add Ouija App files
    [Ouija_Cursor.stl]
2015-07-27 Add objects for Space Explorer app
    [Path.stl, UFO.stl]
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2015-08-28 Solve issues with listeners
    [CoreXY.py]
2015-08-28 Solve issue with cancelling the calibration task not affecting main window
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2015-08-31 Solve bug with toolhead position
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2015-09-08 Solve bug raising exception
    [CoreXY.py]
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2015-09-30 Add demo accesories (screen and controller holders)
    [Electromagnet Controller Holder.fcstd, Electromagnet Controller Holder.stl, Screen Holder.fcstd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]
2015-11-02 Add README for hardware
    [BOM.ods]
